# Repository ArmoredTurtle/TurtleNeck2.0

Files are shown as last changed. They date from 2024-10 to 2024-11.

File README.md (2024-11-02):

# TurtleNeck2.0
TN2_Render
TurtleNeck 2.0 - The smart toolhead buffer.

AT Discord:

Join me on Discord (https://discord.gg/armoredturtle)

TurtleNeck 2.0 (TN2) Is a toolhead buffer for klipper printers designed to work with the [AFC Klipper Add-on](https://github.com/ArmoredTurtle/AFC-Klipper-Add-On).
It ustilizes an STM32G0B1 MCU over usb-c to operate. Making it a single cable addition to your klipper machine.

TN2 utilizes two hall effect sensors to dectect movement of the buffer before hitting a hard stop in either direction. Adiddtionally on the PCB are 5 endstops ports that can be utilized for filament combiners or "hubs".
The purpose of a toolhead buffer such as TN2 is to compensate for mismatched rotation distances between a toolheads extruder and a direct drive AFC ("type 2 MMU" if you like calling them that...)
TN2 uses JST-PH connectors for all of its expansion.

[Build manual HERE](https://armoredturtle.xyz).

#BOM#
| Part  | QTY |
| --- | --- |
| TN2 PCB | 1  |
| 3x2mm magnet  | 1  |
| M2.5x10 FHCS  | 1  |
| ECAS04 bowden collet | 2  |
| M3x8 SHCS | 4  |
| M3x10 FHCS | 2 |
| M3 Heatset insters | 4  |
| 1mm Felt adhesive backed |~1x10mm X4 |

TN2 0 Pins

#Pins of note#
| Device | Pin |
| --- | ----- |
| USB coms | PA11/PA12 |
| Trailing hall effect sensor | PB1 |
| Advance hall effect sensor | PB2 |
| Endstop 1 | PB5 |
| Endstop 2 | PB6 |
| Endstop 3 | PB7 |
| Endstop 4 | PB8 |
| Endstop 5 | PB9 |
| RGB (neopixel) | PD3 |

#Schematic
Schematic_TurtleNeck_2024-10-13

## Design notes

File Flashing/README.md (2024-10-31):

# TN2 Flashing Steps
--------------------------------
```
cd ~/klipper
make menuconfig
```
```
[*] Enable extra low-level configuration options
    Micro-controller Architecture (STMicroelectronics STM32) --->
    Processor model (STM32G0B1) --->
    Bootloader offset (No bootloader) --->
    Clock Reference (8 MHz crystal) --->
    Communication interface (USB (on PA11/PA12)) --->
    USB ids --->
()  GPIO pins to set at micro-controller startup
```
#
TN_Firmware

# 
When the config is complete type 'q' to exit then select 'Yes' to save the config.
Now type 
```
make clean
```
followed by 
```
make
```
to build the Klipper firmware

Verify the TN2 is in DFU mode with 
```
lsusb
```
If you don't see a DFU device hold the boot button and press reset then run the lsusb command again.

### To Flash 
```
make flash FLASH_DEVICE=**Device ID**
```
The prompt **File downloaded successfully** indicates the writing was completed. *There will be error messages following this that say dfu-util:Error during download get_status. This is normal just ignore it.*

After the firmware write is completed run
```
 ls /dev/serial/by-id/
```
to get the device serial ID

Plug this ID into the turtleneckv2.cfg in the serial section

## To Update Firmware
```
cd ~/klipper
make menuconfig
```
```
[*] Enable extra low-level configuration options
    Micro-controller Architecture (STMicroelectronics STM32) --->
    Processor model (STM32G0B1) --->
    Bootloader offset (No bootloader) --->
    Clock Reference (8 MHz crystal) --->
    Communication interface (USB (on PA11/PA12)) --->
    USB ids --->
()  GPIO pins to set at micro-controller startup
```
When the config is complete type 'q' to exit then select 'Yes' to save the config
type 
```
make clean
```
followed by 
```
make
```
to build the Klipper firmware.

### To Flash
```
make flash FLASH_DEVICE=/dev/serial/by-id/**Your device serialID**
```
The prompt **File downloaded successfully** indicates the writing was completed. *There will be error messages following this that say dfu-util:Error during download get_status. This is normal just ignore it.*

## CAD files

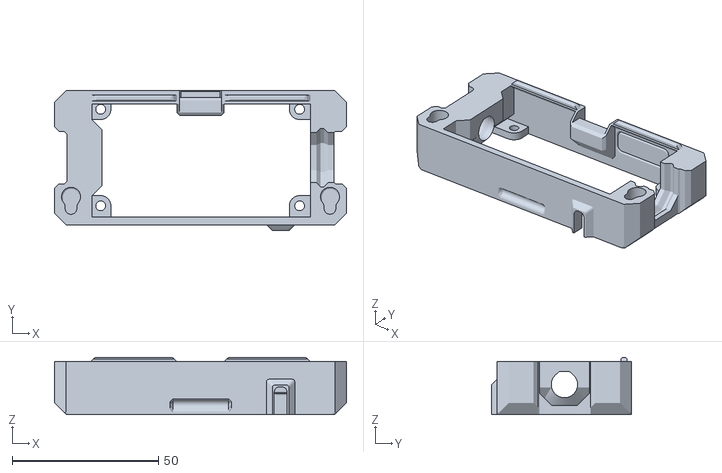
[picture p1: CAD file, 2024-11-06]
TN2_STLs/main_body.stl
99.8 x 48.0 x 19.6

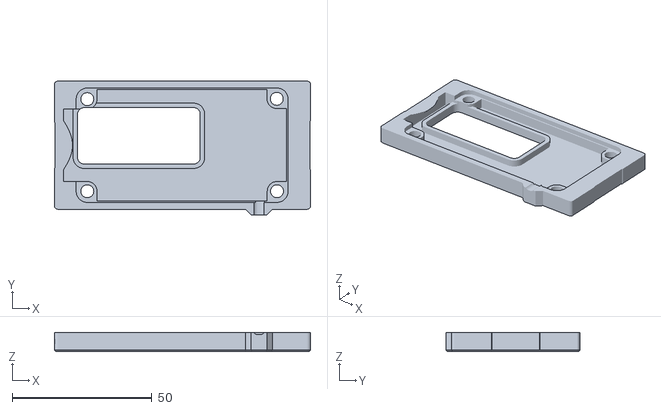
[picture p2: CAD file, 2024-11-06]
TN2_STLs/[a]_baseplate.stl
91.8 x 48.0 x 6.91

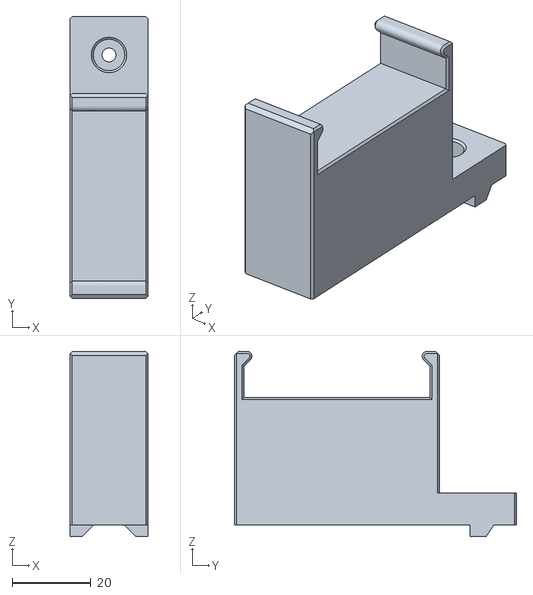
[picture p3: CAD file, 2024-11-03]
TN2_STLs/TN2.0_horizontal_mount_30mm.STL
19.7 x 71.5 x 47.0

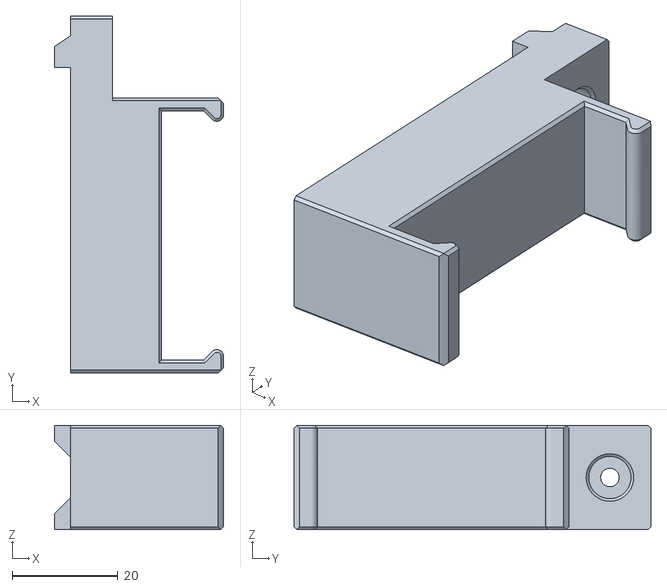
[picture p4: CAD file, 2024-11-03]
TN2_STLs/TN2.0_horizontal_mount_15mm.stl
32.0 x 67.5 x 19.7

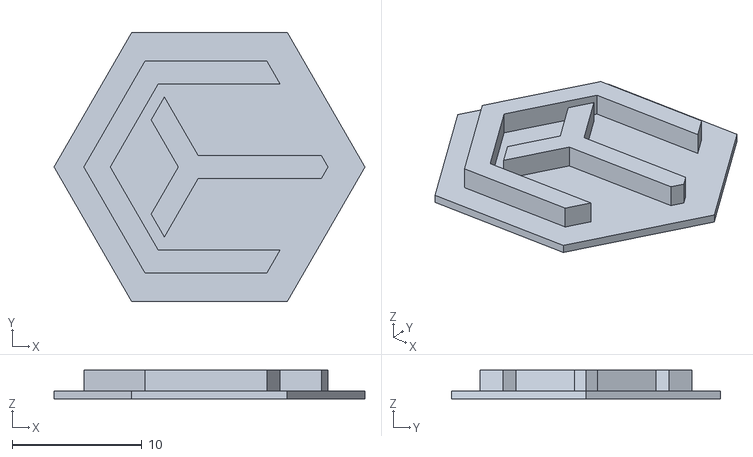
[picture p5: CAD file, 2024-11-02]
TN2_STLs/[c]_inlay_single_piece.stl
24.0 x 20.8 x 2.20

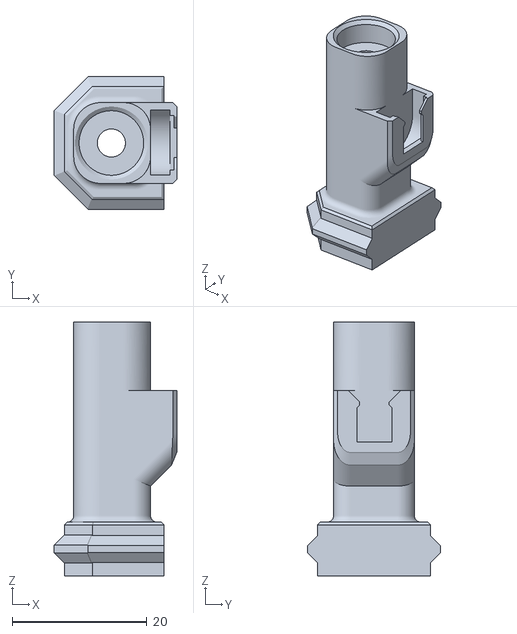
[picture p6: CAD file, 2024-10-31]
TN2_STLs/single_inlet.stl
18.2 x 19.8 x 37.8

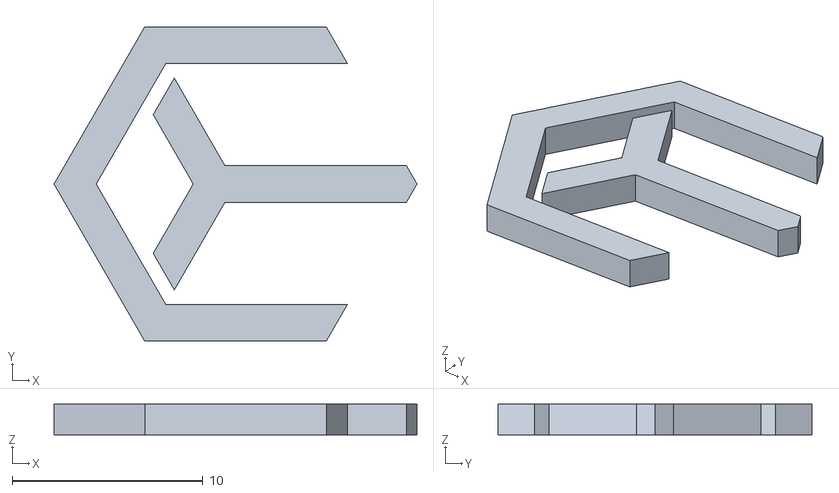
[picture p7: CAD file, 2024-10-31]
TN2_STLs/[c]_logo_inlay.stl
19.0 x 16.5 x 1.60

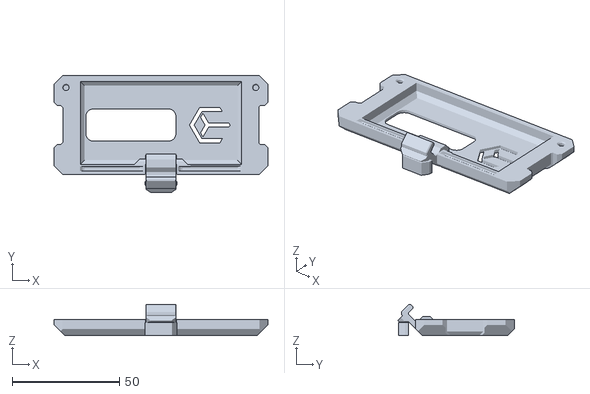
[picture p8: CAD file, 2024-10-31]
TN2_STLs/[a]_lid.stl
99.8 x 54.4 x 14.6

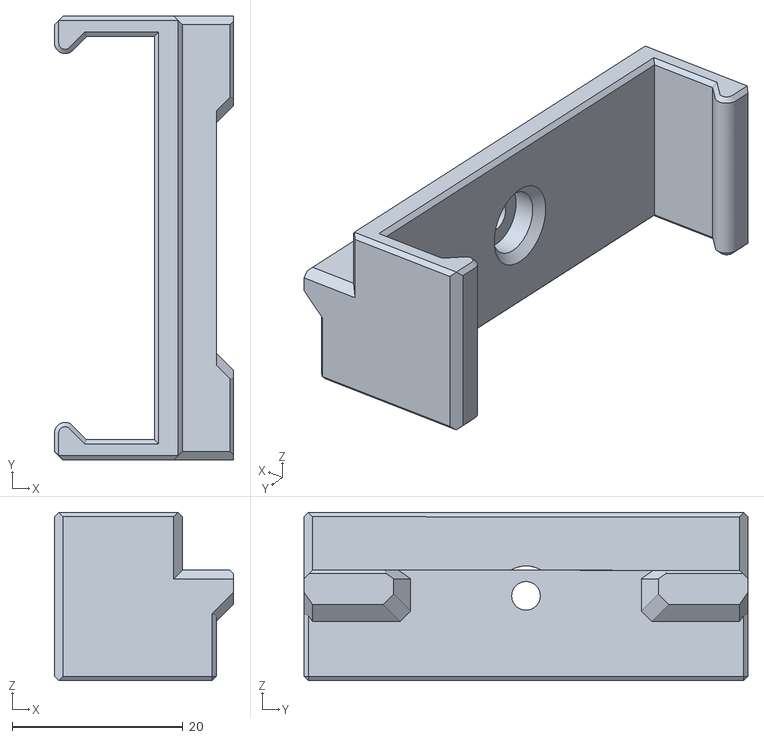
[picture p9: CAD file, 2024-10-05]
TN2_STLs/clip_mount_4mm.stl
21.0 x 52.0 x 19.7

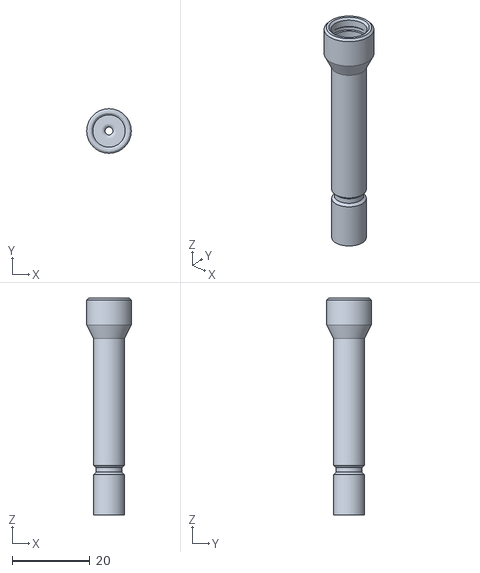
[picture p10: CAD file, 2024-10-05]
TN2_STLs/[a]_tube.stl
11.5 x 11.5 x 56.0

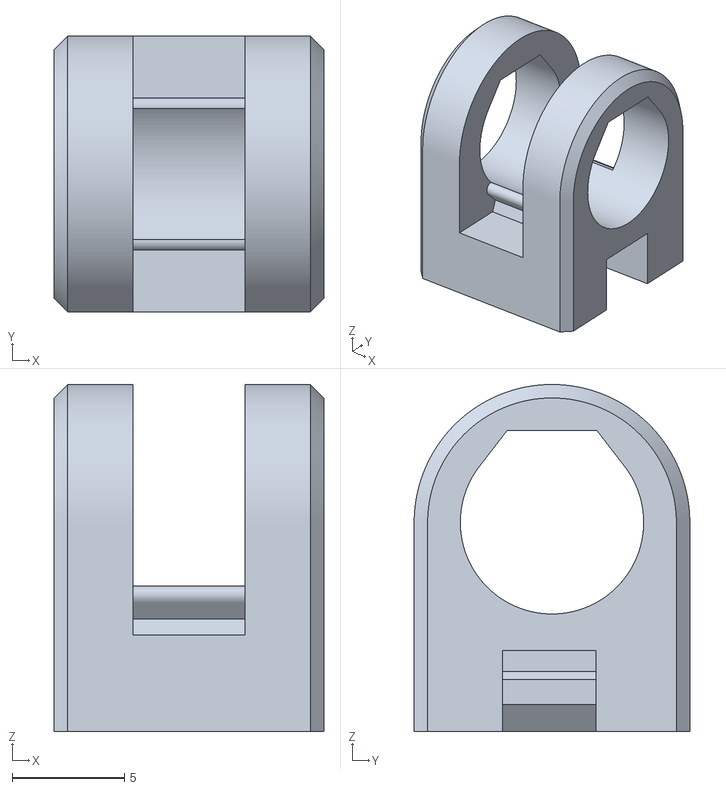
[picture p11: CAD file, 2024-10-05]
TN2_STLs/carriage.stl
12.0 x 12.3 x 15.4

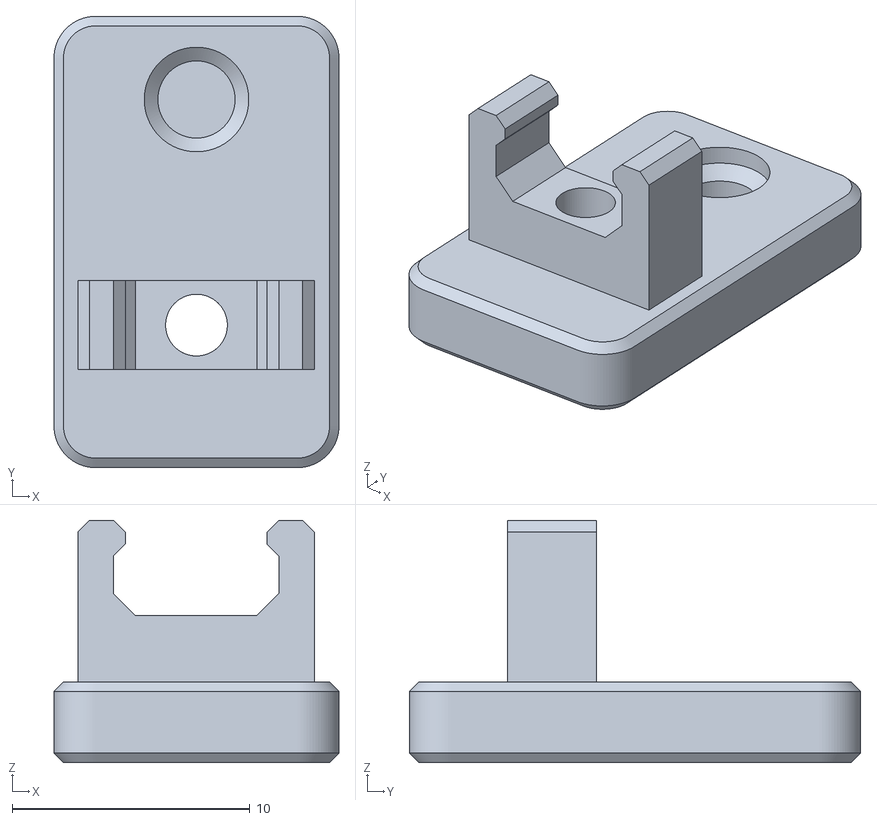
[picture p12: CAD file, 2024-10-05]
TN2_STLs/slide.stl
12.0 x 19.0 x 10.2

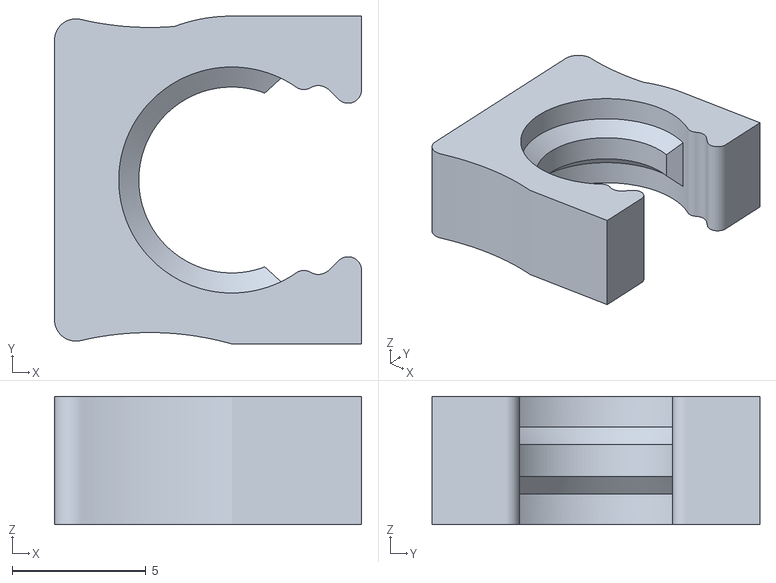
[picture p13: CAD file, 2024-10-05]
TN2_STLs/clip.stl
11.5 x 12.3 x 4.80

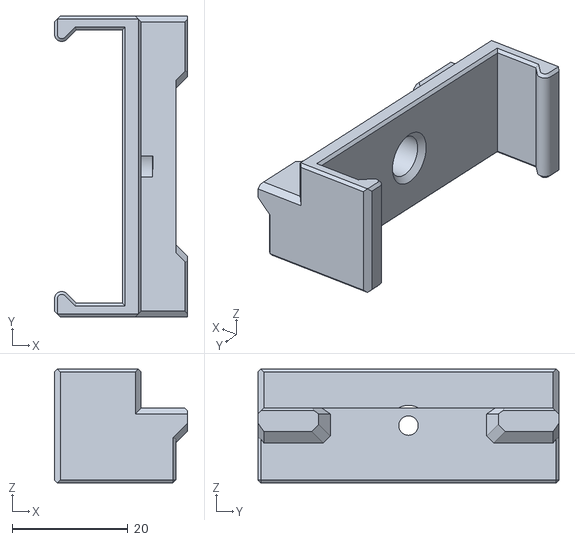
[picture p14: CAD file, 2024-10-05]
TN2_STLs/clip_mount_6mm.stl
23.0 x 52.0 x 19.7

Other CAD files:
TN2_STLs/clip_mount_5mm.stl

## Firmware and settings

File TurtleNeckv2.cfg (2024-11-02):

[mcu turtleneck]
serial: /dev/serial/by-id/**YOUR SERIAL HERE**

[board_pins tn_v2]
mcu: turtleneck
aliases:
  TRAILING = PB1,
  ADVANCE = PB2,

  ES1 = PB5, ES2 = PB6, ES3 = PB7, ES4 = PB8, ES5 = PB9,

  RGB = PD3,

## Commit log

2024-10-07 Added missing magnet
2024-10-28 Update and rename TurtleNeck2.cfg to TurtleNeckv2.cfg
    [TurtleNeckv2.cfg]
2024-11-02 Fix Pin Map
    Fix Pin Map in cfg
    [TurtleNeckv2.cfg]
2024-11-02 Update README.md
    Fix Pin map for advance and trailing
2024-11-06 Updated main_body with a more confined path around the tube for support.
    [[a]_baseplate.stl, main_body.stl]
